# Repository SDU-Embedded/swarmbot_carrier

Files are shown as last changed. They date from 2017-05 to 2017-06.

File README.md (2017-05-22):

# swarmbot_carrier
Repository containing documentation related to the design and operation of the Swarmbot carrier card.

# Revision history
### Rev. 2, May 2017:
* Fixed pinout of the BSS138 MOSFET (A grounded gate pin makes for a boring circuit).
* Swapped the negative and positive inputs on U1 to correctly enable the 3.3V rail. 
### Rev. 1, April 2017:
Initial layout for debugging purposes.

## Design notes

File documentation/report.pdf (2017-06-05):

University of Southern Denmark

MSc in Engineering - Electronics

Individual Study Activity

## Developing the Swarm Bot

Authors:
030192 Mikkel Skaarup Jaedicke 100589 Thomas S. Christensen

Supervisor:
Leon Bonde Larsen

Date: 31-5-2017

## 1 Introduction

A platform for research of flocking behaviour in swarms of robots was developed throughout the bachelor’s thesis, “Investigating Bio-inspired Object Avoidance in a Swarm of Mobile Robots” by Niels A. Hvid and Rasmus
K. Stagsted. Throughout that project an analysis was carried out in order to determine the requirements of the system. This project aims to replace the Raspberry Pi with an FPGA platform, namely a Zynq platform. Using an FPGA/ARM combination is believed to better enable the use of swarm algorithms. Additionally, since the completion of the bachelor’s thesis, a new type of microphone has been procured. This type is digital, as opposed to the previous analogue microphones. Much of the electronics developed for that project is developed so as to work around the shortcomings of the Raspberry Pi, as well as the amplifier circuits required for the microphones. This project will redesign the electronics where necessary in order to accommodate the changes on the platform.

## 2 Analysis

This analysis will seek to expand on the analysis carried out in the aforementioned thesis. Some of the conclusions reached are no longer valid due to the new platform. It is necessary to determine which parts will need redesign and possibly, what new features will need to be added altogether.

### 2.1 Mechanical Platform

The chassis, battery and motors, including their encoders remain unchanged and as such will not be discussed further in this context.

### 2.2 Microphones

As mentioned, a new set of digital microphones has been procured for use with this robot. The previous electronic circuits developed include an amplifier section for the analogue microphones. This is no longer necessary. The analysis did find, however, that the multilateration algorithm is more robust when the microphones are further apart, therefore the new microphones should be placed towards the corners, as was done with the previous microphones.

1

### 2.3 Click Generator

Previously, it was attempted to generate a click using a piezo transducer. The attempt did not manage to produce a sufficiently loud click. A piezo transducer deforms when a voltage is applied to it. A higher voltage increases the deformation. By repeatedly pulsing the transducer with a sufficiently high voltage, it should be possible to generate a sound. Some type of circuit will have to be used to generate the necessary voltage spike.
The sound of a Piezo transducer is amplified when placed in a plastic housing with a small hole to let the soundwaves out. This housing and the size of the hole should be designed to amplify the specific piezo transducer’s resonant freqency. Designing such a housing is infeasable, considering how cheaply a finished product can be procured. A piezo element is generally designed to generate sound with a specific frequency. This can be seen by inspection of the frequency response curve of a piezo transducer. A depiction of a typical response curve can be seen in figure 2.1

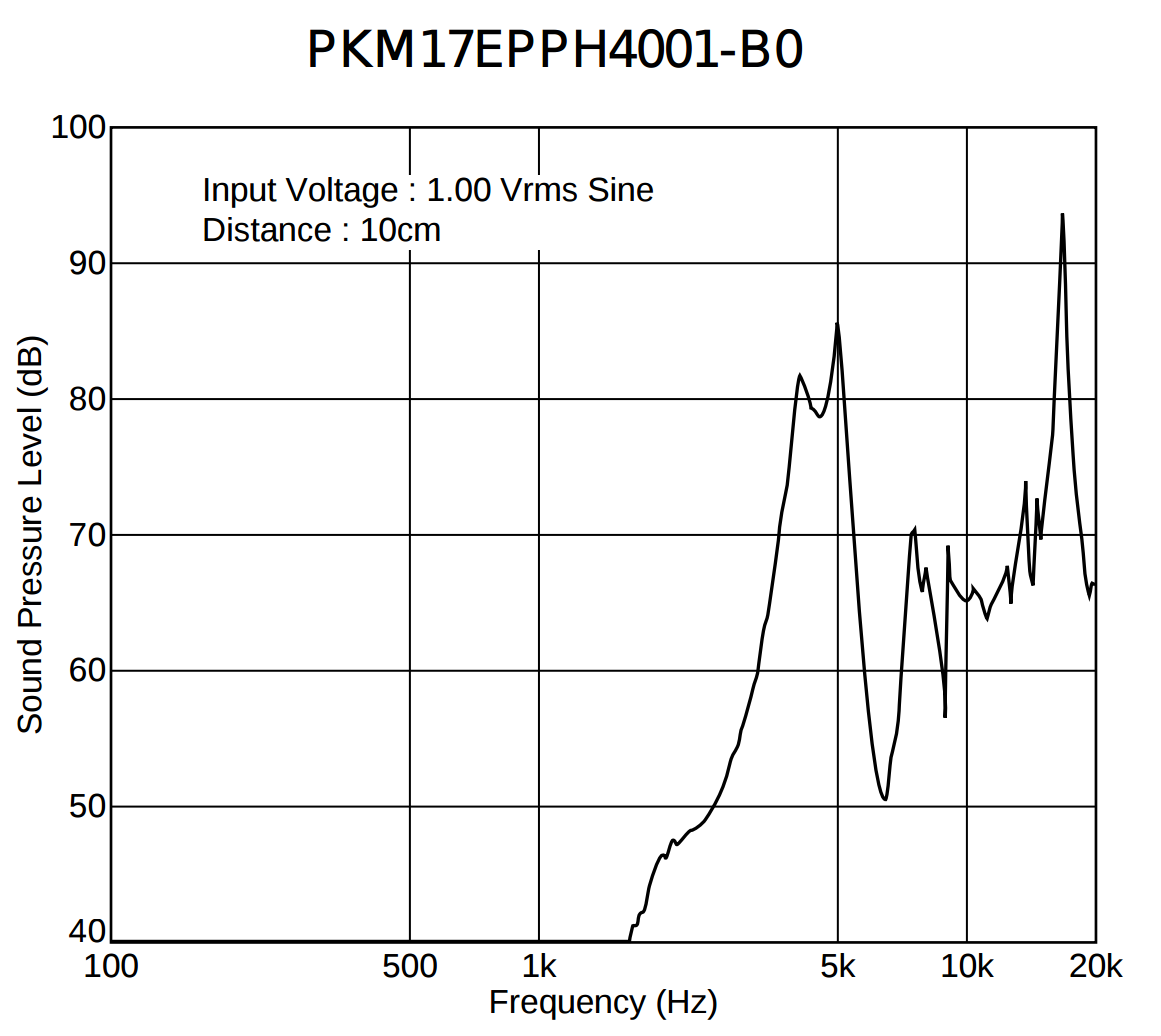
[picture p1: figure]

Figure 2.1: Typical frequency response of a piezo electric transducer. This particular model is most effective at approximately 5kHz and 18kHz.

Generally there are a range of frequencies around the resonant frequency that are at a much higher sound level than the rest of the frequencies. Frequencies not in close range of the resonant frequencies are often attenuated by decades of dB. This makes a normal piezo unfit for generating a click sound as this is approximated by a short frequency sweep. Another option is the piezo speaker that is designed to have the same flat frequency response curve as an ordinary speaker. It is therefore more fit to produce a clicking sound by making a frequency sweep. An ordinary speaker can also

2

be used, but generally they consume much more current to produce the same sound. It was choosen to order three different kinds of sound generators to experiment with sound loudness, clicking sounds and power consumption.

- Piezo element with plastic housing and internal drive circuit [10].
- Piezo speaker in plastic housing without drive circuit [11].
- Miniature speaker [12].

Piezo Element with Internal Drive Circuit

This element produces a sound with a constant frequency just by connecting it to a DC power supply. This is very simply and allows for a minimal interface, but the internal drive circuit makes it impossible to produce a frequency sweep.

Piezo Speaker

This Piezo speaker is designed to have a more flat frequency response and is therefore suitable for producing a frequency sweep. An external drive circuit needs to be developed to test the device as a drive circuit is not included with this product. The developed circuit can be seen in figure 2.2.

D

C

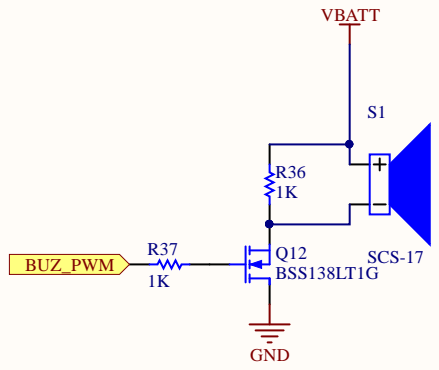
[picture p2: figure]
Q12 BSS138LT1G; SCS-17; VBATT; GND; BUZ_PWM

Figure 2.2: Schematic of drive circuit for piezo speaker.

A mosfet controlled by a PWM pin is toggling current from VBATT to GND and thereby controlling the sound generated by the piezo. By changing the dutycycle of the PWM signal the volume produced can be controlled. A 50%

3

dutycycle yields the highest volume. A resistor is placed in parallel with the piezo speaker as it is capacitive and needs to discharge when the mosfet goes off. The resistor in front of the mosfet is needed to limit the current from the PWM port.
In experiments with the circuit and the piezo speaker, the PWM port was connected to a frequency generator set up to do frequency sweeps. This produced loud and clear clicks.

Miniature speaker

The miniature speaker, as the piezo speaker, needs a drive circuit. The circuit from figure 2.2 was used again and the same frequency generator was used. In this setup the miniature speaker also produces clicks that was audible, but the sound produces was of significantly lower volume. Which was also expected.

Conclusion

It was chosen to use the Piezo speaker with the developed drive circuit as it has the capability of producing a click sound and it produced a significantly greater volume than the miniature speaker in the same setup. Besides that it produces no electro magnetic noise as the miniature speaker does.

### 2.4 PWM Generation

The Raspberry Pi previously used has support only for one PWM channel. In order to fully control the robot, four channels are required. For this reason it was chosen to use an external PWM generator which can be communicated with through I2C. Moving to an FPGA based platform, this is no longer necessary, as it is possible to add as many PWM channels as required in VHDL.

### 2.5 Motor Driver

The BD6222HFP was chosen as the motor driver in the previous project. This is a full-bridge capable of continuously supplying sufficient power to drive the motors on the robot. This driver chip is maintained in the new design.

4

### 2.6 Current Limitations

A number of fuses were added to limit the current to the motors as well as the current draw from the battery. The battery however, includes a “safety board” which limits the maximum possible current draw, making this fuse irrelevant. The fuses on the motors can be excluded by instead running a check in software such that when a voltage is applied, the encoder signal must represent movement, or the voltage will be cut. Allowing overcurrent for a short period will not damage the motors and therefore this approach is acceptable.

### 2.7 Electronics Board

In order to accommodate the new electronics a new board will have to be designed. The board must support a number of components and circuits, listed below.

- Motor controller: The BD6222HFP, a full-bridge motor controller, is used to generate the drive signals for the motors.
- Piezo: Generating a click is done using a piezo transducer. A transducer with an external drive circuit will be used.
- 5V DC/DC Converter: A DC/DC converter will be used to generate the 5V rail necessary to drive the embedded platform.
- Connections: A number of connections has to be present on the board. Passthrough for the microphone add-in board. Passthrough for the motor encoders. Connection for battery.
- Debug LEDs: Support for four LEDs for debugging is required. The necessary drive circuitry must be added.
- Microphone board: A microphone board has been developed at SDU, supporting up to four SPH0641LU4H-1 digital microphones. The board must allow for interfacing with this microphone board.

### 2.8 Power Calculations

In the previous project it was chosen to use linear regulators to supply the 5 and 3.3V rails. This project will analyse whether the added cost of using switch-mode converters is worthwile considering the possible extra battery life. It will be analyzed how much power is drawn from the 5V- and

5

battery voltage-rails and what the expected additional battery life will be when using a switch-mode converter. It has been found that the DC/DC converter, PTH08080WAH, is suitable for this project and this component’s specifications will be used for calculations.

5V Rail (VCC)

The following are powered by VCC:

- Microphones including circuitry, 11mA
- Zynqbased embedded platform, 500mA
- Two motorcontrollers, 5mA
- Six LEDs, 120mA

The current estimation of the microphones, motorcontrollers and LEDs are based upon datasheet values. Whereas the current estimation for the Zynqbased platform is based upon current measurements from a previous project. The current drawn of the Zynq is obviously dependent on the program running, the amount of logic in use, the number of GPIO in use and so on. All of these are unknown at time of writing. 500mA is by no means the maximum current draw that can be expected from a Zynqbased platform, as the MicroZed draws 1.7A at 85% utilization [4].
These estimates bring the total current draw of the VCC rail to 636mA

Battery Voltage Rail (VBATT)

The motors will be running directly from VBATT. To measure the current drawn by the motors and motorcontrollers a small test was conducted. Three different voltages were applied to the motors using a laboratory power supply. Voltage and current measurements were made with the robot driving. The results are shown in table 2.1.

Table 2.1: Voltage, current and power of motors and motorcontrollers measured at different velocities.

Velocity | Voltage, [V] | Current, [mA] | Power, [W]
Low | 1 | 220 | 0.2
Medium | 5 | 305 | 1.5
High | 8 | 350 | 2.8

6

The piezo speaker is powered by VBATT as well, but it produces sound only for a few milliseconds at a time and in addition, with a very power. For this reason, this current draw is neglected throughout the remainder of the discussion.

Power Dissipation

When using a linear voltage regulator the power dissipated in the component can be calculated using:

PLR = (Vin − Vout) · Iload

The power dissipation in the linear regulalator can be found using the current estimation at 5V and the fact that the battery has a nominal voltage of 7.4V:
PLR = (7.4[V ] − 5.0[V ]) · 0.636[A] = 1.5[W]

If a switching regulator is used the voltage conversion will have a significantly higher efficiency. The pth08080w has a typical efficiency of 93.5% at 5V [6]. The power dissipated in the DC/DC converter would be:

PSW = Vin · Iload · (1 − η)

PSW = 7.4[V ] · 0.636[A] · 0.065 = 0.3[W]

The total power drawn at the 5V rail is:

P5V = 0.636[A] · 5[V ] = 3.2[W]

Based on the measurements of voltages and currents of the motors and motorcontrollers, the power dissipated were calculated to be as in table 2.1. The total power usage can be calculated as the sum of the combined powers.

PT = Preg + Pmotor + P5V

Calculating the total power usage at low velocity and using a linear regulator yields:
PT,LR = 1.5 + 0.2 + 3.2 = 4.9[W]

The total power at the three velocities is calculated using a linear regulator or a DC/DC converter and is shown in table 2.2.

7

Drive Time

The amount of energy the battery can store should be calculated in order to calculate the drive time of the robot. The batteries have a rated capacity of 2600mAH [9]. Converted to Joule:

Ebat = 2.6[AH] · 7.4[V ] · 3600 = 69.3[kJ]

The drive time can then be calculated:

T =

Ebat
PT

Specifically for low velocity and using a linear regulator:

TLR =

Ebat

PT,LR

=

69.3[kJ]
4.9[W]

= 14143[s]

Which corresponds to 3.9h. The calculation is done for all scenarios and the results are shown in table 2.2. Finally the extra drive time obtained by using a switching regulator rather than a linear regulator is calculated and shown in percent in table 2.2.

Table 2.2: Total power and drive times using linear regulator or switching regulator. The obtained extra drive time by using a switching regulator is given in percent.

Velocity | PT,LR [W] | PT,SW [W] | TLR [h] | TSW [h] | % more T
Low | 4.9 | 3.7 | 3.9 | 5.2 | 33
Medium | 6.2 | 5 | 3.1 | 3.8 | 23
High | 7.5 | 6.3 | 2.6 | 3.1 | 19

Using a switching regulator yields a minimum of 19% more drive time compared to using a linear regulator. On the basis of the results it is concluded that using a switching regulator is worth the additional cost.
Note that these results are very conservative estimates. The more power is being drawn from VCC, the more the benefits if the switch-mode converter would show.

### 2.9 Embedded Platform

Previously a Raspberry Pi was used to power the platform. As mentioned, it has been requested that the system is ported to a Zynq platform. Currently

8

available to the authors are the Zybo, MicroZed and Zynqberry platforms. All three are based around the Zynq-7010 chip. A number of GPIO ports are required; seven pins for PWM for the motors, four pins for encoders, four pins for microphones, one for a piezo transducer and six for two RGB LEDs. This amounts to a minimum of 22 pins required. Below is an overview of the pros and cons of the two platforms.

- Zynqberry: As the name implies, this platform is made to conform with the physical layout of the Raspberry Pi. Using this platform would allow the reuse of the mounting solution developed for the Raspberry Pi. At 26 total GPIO pins, the Zynqberry can supply the required GPIO, but has nearly no pins if extra sensors or hardware is needed in the future. When searching for information on this platform it was found that there is not a lot of documentation made by neither the manufacturers or the community.
- Zybo: This platform is significantly larger than the Zynqberry. The different form factor requires that a new mounting solution is devised. Additionally, the increased size means that the board will have to be mounted above the tracks to avoid interference. While this is an inconvenience, it should not pose an issue in collisions as the edges of the board are still within the bounds of the robot. At 48 total GPIO pins, the Zybo can supply the required GPIO.
- MicroZed: This platform is within the confines of the robot platform, but has a different formfactor than the Raspberry Pi and therefore the mounting solution would need a re-design. It can be used as a stand-alone evaluation board, but needs to be combined with a carrier card if the PLs I/O pins are to be used. This is because the I/O banks on the Zynq chip need external powering, supplied by the carrier card. The 100 I/O pins on the MicroZed are accessed through two micro headers. The company behind the MicroZed also ship different carrier boards that can be used. If a custom carrier board is needed, circuitry for control signals and power needs to be developed. The online documentation for the MicroZed and carrier card is thorough and plentyfull including user guides, hardware guides, schematics and bill of materials.

The MicroZed is found to be the best choice for this project. Mainly because it is within the confines of the robot platform, gives access to 100 I/O pins and has solid documentation.

9

MicroZed Carrier Card

It was decided to design a custom carrier card for the MicroZed. A number of the requirements, which are outlined in this section, would result in additional boards having to be connected to the Avnet carrier cards anyways and so it was decided to combine all of the functionality on one board. As mentioned, this section will define the requirements for the MicroZed carrier card to be designed. Avnet provides a carrier card design guide [1] that describes some of the requirements. It describes how to utilize the Zynq chip on the MicroZed board. In this project, only a number of general I/Os are needed. Two ADCs are added for the possibility of utilising them at a later stage. This carrier card however, is expected to be used across a number of other, yet undefined projects. For this reason the card is designed in a more general fashion, rather than specifically for the swarmbot. Below is a list of the features the carrier card is designed to support.

- ADC, not used on the swarmbot.
- Motor Drivers capable of driving the swarmbot.
- Support for the digital microphone board, developed at SDU.
- Support for click generator.
- Passthrough of MicroZed GPIO.
- Debug LEDs.

These points are the features that the user will be presented with when using the board. In addition to these, a number of requirements are set in the afforementioned design guide:

- Anti-aliasing filters for ADC inputs.
- Power for MicroZed board and Zynq I/O banks 34 and 35.
- Correct power sequencing on boot/shutdown.
- Microheader connection to MicroZed.

The following sections will outline how each of these points are addressed in the design of the carrier card.

10

## 3 Design and Implementation

Avnet supplies a MicroZed breakout carrier card as a reference design for designing carrier cards. All of the schematics and layout documents are made publicly available and will, in conjunction with the carrier card design guide [1] form the basis for the design of the swarmbot carrier card.

### 3.1 Power Requirements

A carrier card needs to provide the following voltages for the MicroZed:

- Vin = 5V
- Vccio,13 (Voltage logic level for I/O bank 13)
- Vccio,34 (Voltage logic level for I/O bank 34)
- Vccio,35 (Voltage logic level for I/O bank 35)

The different I/0 banks can be operated at different voltage levels. According to [2], the possible logic levels are 1.2V, 1.5V, 1.8V, 2.5V, and 3.3V.
It was chosen to supply all I/O banks with a voltage level of 3.3V as the vast majority of hardware used is available at this voltage. Additionally, it simplifies both the circuitry, as well as the use of the board.

Vccio = Vccio,13 = Vccio,34 = Vccio,35 = 3.3V

The schematic and components used for the generation of the 3.3V rail is available in [3] and [13] and will not be discussed further as this is not the design of the authors. Since the swarmbot is designed to be powered from a 7.4V LiPo battery, the 5V rail has to be generated from this rail. As the voltage of a battery is not static, the converter will have to be able to supply the required voltage throughout the entire discharge cycle. In order to determine the maximum and minimum voltages of the battery, a discharge curve was created. More detail on the test done to create the curve can be found in section 4.3, but the result is repeated in figure 3.1 for convenience. Here it can be seen that the maximum voltage once fully charged is 8.4V while the minimum voltage when discharged fully is approximately 5.5V, as per the documentation of the battery [9]. Attempting to procure a DC/DC converter capable of maintaining a stable 5V output with an input voltage of just 0.5V higher may prove to be an expensive endeavour. The curve reveals that the voltage remains above 6V for ≈85% of the discharge cycle, even when discharging at 4A, far above what the carrier card will be capable

11

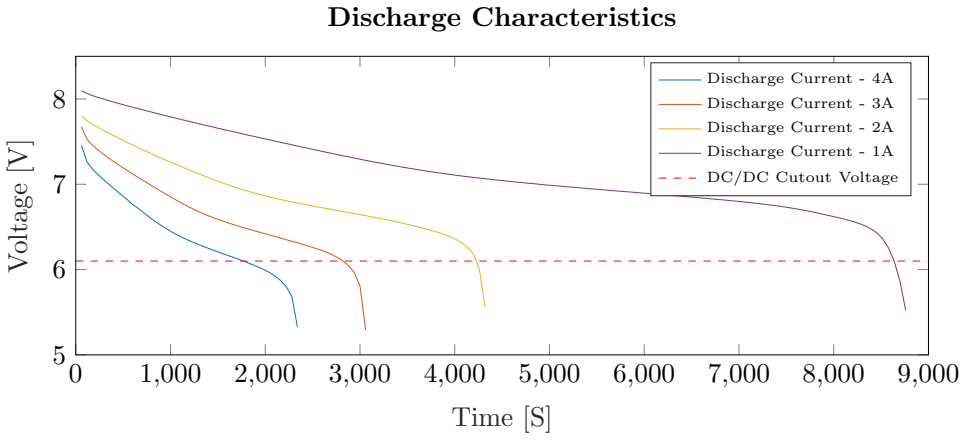
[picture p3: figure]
Time [S]; Voltage [V]; Discharge Characteristics; Discharge Current - 4A; Discharge Current - 3A; Discharge Current - 2A; Discharge Current - 1A; DC/DC Cutout Voltage

Figure 3.1: Discharge curve of the Ansmann 18650 2S1P Li-Ion battery used to power the swarmbot.

of handling. For this reason, this will be the target minimum input voltage of the DC/DC converter. According to [4] the estimated maximum power draw of the MicroZed is 1.7A at 5V. This is assuming 85% utilisation of PL and a conservative 80% efficiency of the converters. The estimate made by Avnet is made with the Zynq-7010 in the Xilinx Power Estimator (XPE) [5]. The MicroZed used for the swarmbot project, however, is equipped with the Zynq-7020, a slightly larger chip. Running the same scenario, 85% utilisation, in XPE reveals that the 7020 draws 2.3W, just 0.1W more than the 7010, a marginal difference in the total power budget. In addition to the MicroZed, also the debug LEDs and the microphone board are powered from this rail, adding an estimated ≈150mA extra current draw. In summary, these are the requirements for the DC/DC converter used for generating the 5V rail:

- Must function across the entire voltage range of the battery, 6V to 8.4V.
- Should be able to supply at least 1.85A at 5V.

Below is a discussion of the various choices made in the design of the circuitry of the 5V supply.

12

Designing the 5V Rail

The PTH08080WAH [6] closely meets these requirements at a maximum power delivery of 2A/10W/5V. The device is designed to have a wide input range, accepting Vin=Vo+1.1V to 18V. At the required 5V this translates to an input range of 6.1V to 18V. This is of course slightly higher than the desired 6V, but even at the maximum discharge rate, estimated at 2.2A-2.3A, with the MicroZed drawing its maximum current and the motors running at full speed, there would still be approximately 70 minutes of operation per charge. Vo is determined via an external resistor Rset. A formulae is provided to calculate the exact Rset needed for a given voltage, however a large table of common values is already calculated. According to this table, Rset=353Ω results in 5V. 353Ω is not a standard value, choosing 348Ω instead yields 5.01V, which is fine for this application.

The circuit appertaining to this component can be seen in figure 3.2. This is the standard application circuit as shown in the datasheet (figure 10 [6]). According to the datasheet, the minimum recommended input capacitance is 100µF. Of the capacitors on the list of recommended capacitors, also given in the datasheet, the 20SVP150M was chosen. It is rated for 20V, sufficient for this application, and has a capacitance of 150µF.

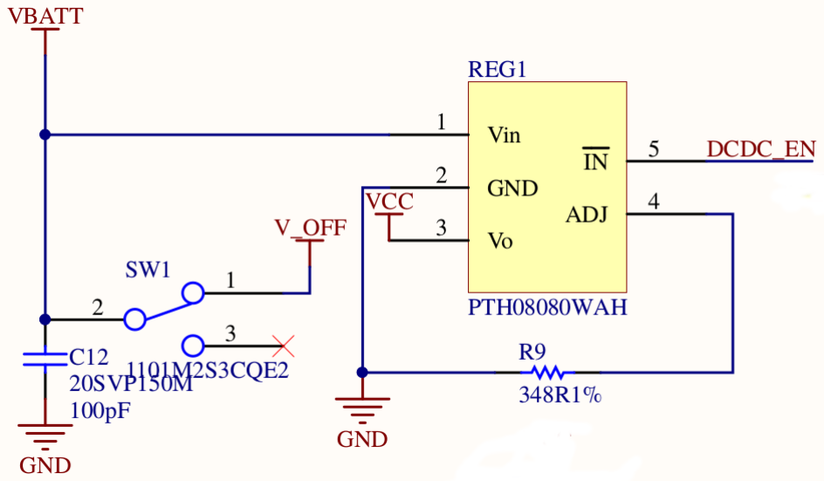
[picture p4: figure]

Figure 3.2: Circuit for generating VCC, the 5V rail.

### 3.2 Power Up Sequence

According the carrier card design guide, [1], a carrier card needs to adhere to a specific power up sequence in order for the MicroZed to turn on correctly. On power up, MicroZeds PWR EN signals need to be pulled high on the carrier card, to enable power to the MicroZed. This is done with a pull-up resistor

13

as shown in figure 3.3.

38LT1G

EN

100nF

C18
C0805

Q2
BSS138LT1G

GND

VCC

GND

V_OFF

POWER_EN POWER_EN

D4

18TQ045

R12
1K

R15
3K92 1%

R20
430R 1%

R19

680R 1%

Figure 3.3: Circuit for proper power sequencing on MicroZeds PWR EN.

When the MicroZed has powered up its internal DC/DC converters and is ready to receive voltage on its I/O banks VCCIO EN will go high. VCCIO EN has a logic level of 1.8V and the signal is therefore fed to a comparator that outputs a 5V signal to a DC/DC converter when VCCIO EN is high. The DC/DC converter is configured to produce a voltage level of 3.3V that is connected to VCCIO. This circuitry can be seen in figure 3.4.

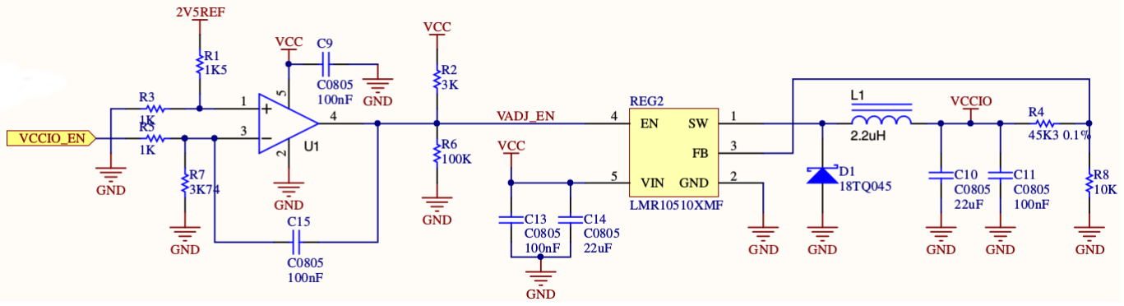
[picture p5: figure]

Figure 3.4: Circuit for proper power sequencing on I/O banks.

### 3.3 Power Down Sequence

A power down sequence is also described in [1], that needs to be followed to ensure signal integrity while powering down. The signals VCCIO EN, DCDC EN and PWR EN should be pulled down in that order when powering off. The

14 signals are pulled down by mosfets controlled by the V OFF signal. When the power switch on the carrier card is in off mode, the battery voltage is connected to the V OFF rail thereby turning the mosfets on and pulling the signals down. The correct sequence is maintained by charging capacitors on the gate side of the mosfets thereby creating a delay. Such a mosfet circuit is shown in figure 3.3.

### 3.4 Analog to Digital Converter

The Zynq 7-series FPGA’s are equipped with a dual, 12 bit ADC, yet has only one dedicated analog differential pair, VP 0 and VN 0. See figure 3.5 for an overview of the XADC architechture If more ADC channels are needed, any of the 16 auxiliary analog inputs (AAI) can be used. These are placed on I/O bank 35 which, as the rest of the I/O on the swarmbot carrier card, is supplied with VCCIO=3.3V. Once selected, a multiplexer applies each signal to the ADC’s in turn. For this reason any signal on the AAI can never go above VCCIO to avoid damaging the inputs. On the swarmbot carrier card the dedicated analog pins, as well as three AAI pairs are routed to the ADC header (CON4). The signals VAUX P0 and VAUX N0 on JX1 are the dedicated analog inputs and can be used on its own. The remaining three pairs are AAI and must be multiplexed if the user wishes to use them. It should be noted that due to the anti-aliasing filters, these pairs cannot be used as digital I/O on the swarmbot carrier card. These anti-aliasing filters are required in order to filter out high frequency noise in the differential pairs and should be placed as closely to the Zynq as possible, in this case, that is next to the connectors JX1 and JX2, the main connectors to the MicroZed. Figure 3.6 from [?] illustrates a simple measurement setup and the anti-aliasing filter. R1 and R2 form a voltage divider, creating a 1V signal. R5 is matched to the parallel impedance of R1||R2. Resistors R3, R4 and the capacitor C1 can be adjusted to change the settling time of the circuit. [7] gives equation 3.1 which can be used to calculate the settling time and by that determine the maximum sampling frequency.

Ts = ln 2resolution+1
·
R1 · R2
R1 + R2

+ R3 + R4 + R5

·C1 = 4.9 · 10⁻⁶
[S] (3.1)

### 3.5 Buzzer Solution

As described in section 2.3 it was found that the best solution for creating a clicking noise on the platform was to use a piezo speaker with a drive circuit

15

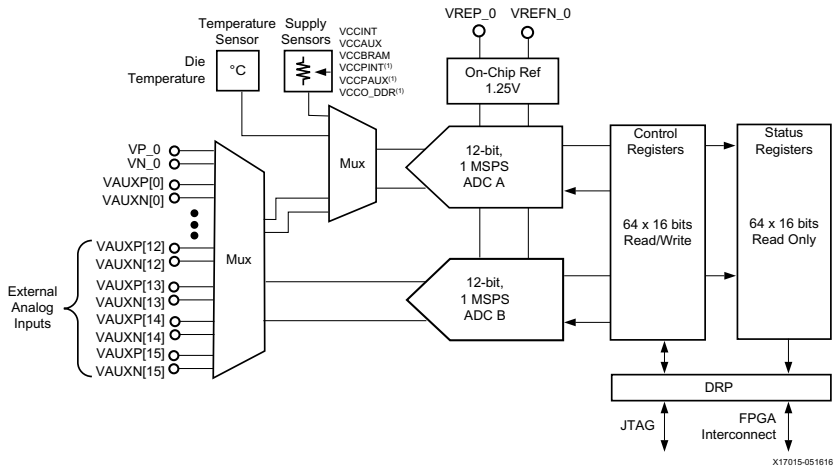
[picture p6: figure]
X-Ref Target - Figure 1-1; 'LH 7HPSHUDWXUH; 7HPSHUDWXUH 6HQVRU; 6XSSO\ 6HQVRUV; ELW 0636 $'&$; ELW 0636 $'&%; [ELWV 5HDG:ULWH; [ELWV 5HDG2QO\; &RQWURO 5HJLVWHUV; 6WDWXV 5HJLVWHUV; 2Q&KLS5HI 9; ,QWHUFRQQHFW; ([WHUQDO $QDORJ ,QSXWV

Figure 3.5: XADC Block Diagram from Xilinx ADC userguide [7].

and a PWM signal. But because there has been made no further investigation into what sound level is needed and what the frequency spectrum of the generated click is, it was decided to leave the circuitry out of the carrier card. Furthermore the sound source should be placed in the center of the robot to ease localization of the robot, but the design of the carrier card did not allow this. Therefore it was decided to include a header providing access to two IO ports, ground and VBATT. The header is shown in figure 3.7. Two IO ports are needed if differential drive of the piezo is wanted. Two holes were added to the carrier card to allow for fixture of the external piezo and drive circuit.

### 3.6 Pinout

The complete pinout can be found at [15] but a few cases are mentioned here for completeness. Some pins on the GPIO headers, (CON5, CON6) are routed to multiple locations, this increases the amount of available IO, but also introduces some possible traps for the user. Below is a list outlining the pins in question.

- MIC *: All of the ports related to the microphone board are routed both to the microphone header, CON3, and one of the GPIO headers, CON5. These ports should not be used as IO if the microphone board is connected.

16

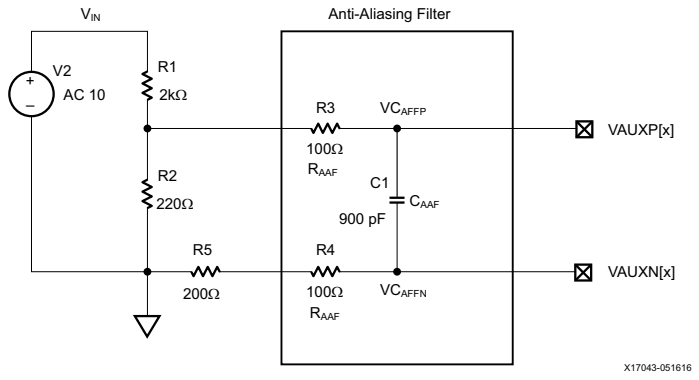
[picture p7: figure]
X-Ref Target - Figure 6-3; VIN; Anti-Aliasing Filter; RAAF; VCAFFP; VCAFFN; CAAF; VAUXP[x]; VAUXN[x]

Figure 3.6: Anti-Aliasing diagram from Xilinx ADC userguide [7].

1
2
3
4

P4

Audio Header

BUZ_PWM1
BUZ_PWM0

VBATT

GND

Figure 3.7: Audio header on the carrier card.

- ENCxy: These ports are wired to both the CON1 or CON2 for channel 0 and 1 respectively, and CON6. The connection to the GPIO header is for measurement only.
- Mx PWMy: These ports are wired directly to the motor controller and should not be used as IO. The connection to the GPIO header, CON6 is for measurement only.
- BUZ PWMx: These signals are wired to the audio header, P4, and to one of the GPIO headers, CON6. These ports should not be used as IO if a buzzer is connected.

In addition to these signals it should be noted that the four signals marked JXx TPyy are meant as test signals. They are GPIO ports but are placed on a seperate header to allow for easier access with measurement equipment.

17

### 3.7 Choice of Components

As mentioned, the choice of components is largely based upon the Avnet carrier card. Generally the same components were chosen but due pricing, availability or minimum order size, some components were changed to similar ones. Table A.1 and A.2 in appendix A explains what components were chosen and why.

### 3.8 Swarmbot Carrier Card Layout

The layout of the swarmbot carrier card was done using Altium Designer. From an early stage it was decided to have the board manufactured by a professional outlet as this would both greatly ease the layout process and, hopefully, minimize the potential points of failure in debugging process. The former, a simpler layout process, is expected for a number of reasons outlined below:

- Mutlilayer Board: Due to the size constraints of the board it is desirable to minimize the number of traces that are required to be routed on the board. Creating a 4-layer board means that the two middle layers can be GND and VCC, allowing every connection to either of these plains to be done using a simple via.
- Feature Size: The manufacturing method used at SDU is not reliable at tracewidths below 20mil and all vias must be drilled by hand, resulting in signal traces being far wider than what is actually required. The manufacturer used to produce the swarmbot carrier card [8] allows traces as low as 8mil and vias at 12mil.
- Plated Vias: The vias created by the manufacturer are plated with copper, meaning that, when using throughhole components the trace can be routed on both the top and bottom layers, without the use of additional vias. This greatly reduces the number of vias required for the layout.

Finally, as was alluded to in the previous paragraphs, the manufacturing process at SDU is not particularly robust and often requires several attempts before the correct combination of incantations, candles and luck is found and a fully functional board is created.

The board has three trace widths: 40mil for VBATT, 20mil for VCCIO and 8mil for the remaining signal wires. Mostly, the size of the board is due to

18 the number of connectors that are required. For this reason there is plenty of room for components and generally capacitors and resistors were chosen with a 0805 footprint. The anti-aliasing filters described in section 3.4 are required to be placed close to the Bergstak connectors (the connector for mounting the MicroZed), which has a 0.8mm pitch. Using 0805 components here is infeasible due to size and it was decided to use 0402 instead.

## 4 Verification

Throughout this section the verification of voltage-rails, desired power-up and power-down sequences are made in order to avoid damaging the MicroZed when first connecting it. After these steps, the correct functionality of the MicroZed while connected to the carrier card is verified. In addition, the functionality of the different IO ports on the carrier are verified to ensure that the carrier card functions as expected. This section will describe the work done to debug and verify the functionality of the carrier card.

### 4.1 Carrier Card Debugging

After soldering of all the components it was found by measurement that the board was not functioning correctly. The debugging of the board will be described in this section.
The carriercard is designed to allow for measurement of the voltage-rails on the powerheader, P1, without connecting the MicroZed. Specifically the J1 jumper should be present to simulate the VCCIO EN signal from the MicroZed. All voltages on the powerheader were measured with an oscilloscope whilst toggling the power switch. VCC should switch between 0V and 5V, which it was not, leading to the conclusion that the circuitry handling the enable signal, DC/DC EN, to the REG1 DC/DC converter could be faulty. By inspection, it was found that the footprint of the mosfets Q1,Q2 and Q3 was wrong. A temporary fix was done by rotating the components, soldering them in place using signal wires. The power switch now toggled both the VCC rail and the 2.5V rail on and off.
Measurements of VCCIO during powerup showed that it immediately went to approximately 3.3V, but then discharged slowly towards zero voltage. The enable signal, VADJ EN, was low even though the input voltages were measured to be as expected. This lead to a thorough examination of the component and the schematic and it was found that the input signals should be switches. The input signals were switched, which fixed the issue and made the VCCIO voltage follow the position of the powerswitch.

19

Measuring the voltage level of VCCIO showed it to be 3.4V rather than the expected 3.3V. This was due to placing a 47kΩ resistor as R4 instead of a 45.3kΩ as specified in the schematics. Even though 3.4V is within spec, it was decided to parallel the 47kΩ resistor was with a 1.5MΩ resistor to yield a resistance of 45.6kΩ and a voltage of 3.33V.

### 4.2 Carrier Card Power Sequencing

As described in sections 3.2 and 3.3 the carrier card is designed to provide a specific power sequence on startup and shutdown.

Startup

To verify the proper startup power sequence of the Swarmbot carrier card the signals VCC, 2V5REF, VCCIO EN and VCCIO were measured and plotted in figure 4.1a. [1] dictates that POWER EN signal must be pulled high on powerup, which was measured to be true. VCCIO EN is produced by the MicroZed and is plotted in figure 4.1a. It can be seen that VCCIO EN rises to its logical level, 1.8V, then goes low for a while and hereafter goes high, which is not the expected behavior. To determine if this behavior was caused by an issue on the Swarmbot carrier card the value of VCCIO EN on the AVNET carrier was measured at startup when connecting the MicroZed to the AVNET carrier card. The two measurements of VCCIO EN at startup is plotted in figure 4.1b. It can be seen that the two datasets are nearly identical concluding that the Swarm and AVNET carrier card yields the same behavior. As VCCIO EN has the same behavior when connecting the MicroZed to the AVNET carrier it is believed to be non problematic.
The converter providing VCCIO should be enabled by VCCIO EN. By inspecting figure 4.1a it is verified that when VCCIO EN is high the converter providing VCCIO is enabled and VCCIO rises towards its final level of 3.3V. It is also verified that 2V5REF reaches its expected voltage level of 2.5V.

20

0 | 2 | 4 | 6 | 8
| | | | ·10⁻³

0

2

4

6

8

Time [S]

Voltage [V]

Startup Sequence, Swarmbot

VCC

2V5REF

VCCIO EN

VCCIO

(a) Signals on the Swarm carrier card at startup.
0 | 2 | 4 | 6 | 8
| | | | ·10⁻³

0

2

4

6

8

Time [S]

Voltage [V]

Startup Sequence, VCCIO EN

VCCIO EN, SWARM

VCCIO EN, AVNET

(b) VCCIO EN at startup on Swarm and AVNET carrier card. Data is shifted in time for clarity.

Figure 4.1: Measured signals at startup.

Shutdown

To verify the proper shutdown power sequence of the Swarm carrier the signals POWER EN, DCDC EN, VCCIO EN and V OFF were measured and plotted in figure 4.2. V OFF switches from 0 [V] to the battery voltage, when setting the power switch in off mode. Then the signals VCCIO EN, POWER EN and DCDC EN should be pulled low in that order. Figure 4.2 shows that to be true.
It should be noted that figure 4.2 only shows the first few microseconds after toggling the power switch. In figure 4.3 the first millisecond is shown and it can be seen that the switch creates quite a lot of bouncing on V OFF. The bouncing could be removed by designing and inferring a low pass filter to the circuit, possibly with a Schmitt trigger circuit to generate a clean edge. This, however, adds additional cost and complexity to the board. Until deemed necessary, this will not be explored futher.

### 4.3 Discharge Curve of the Ansmann 2S1P

In an effort to quantify the possible runtime of the system, a discharge curve was made for the Ansmann 2S1P Li-Ion battery used in this project. Making the discharge curve was done by fully charging the battery using the

21

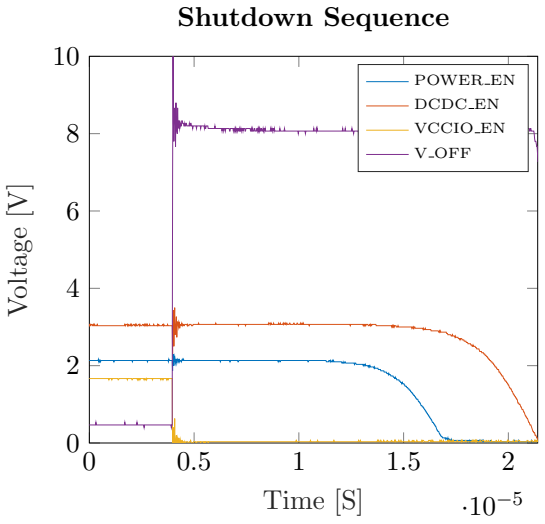
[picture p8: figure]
Time [S]; Voltage [V]; Shutdown Sequence; POWER EN; DCDC EN; VCCIO EN; V OFF

Figure 4.2: Measured signals on the Swarm carrier card at shutdown.

Swallow AC/DC 2 charger. This charger is capable of charging a variety of batteries, following the specific charge curve for each technology. As is expected from a 2-cell Li-Ion battery, the no-load voltage once fully charged is ≈8.4V. After charging, the battery is connected using a DC Electronic Load (model number: EA-EL 3160-60). The load is set at constant current mode and the current set. The battery is equipped with undervoltage protection that turns off the output once the voltage dips below 5-5.5V, in spite of this, it was decided to calculate the theoretical duration and run the test for that amount of time. At 2600mAh it will take 2600mAh/4000mA = 0.65h or, in human terms, 39 minutes, to discharge the battery. For the sake of completion, the trial is repeated for 4, 3, 2 and 1A. The result can be seen in figure 4.4. As discussed in sections 2.8 and 3.1, the maximum current draw of the platform at the battery is approximately 2.2A. Although it should be noted that this is a theoretical maximum and that it is unlikely that this will actually be reached.

As with any battery, due to the internal resistance of the battery the voltage seen at the terminals depends heavily on the current being drawn. The platform will remain functional so long as the voltage remains above 6.1V, the minimum voltage required to maintain VCC, the rail supplying the MicroZed. The maximum speed of the motors will however decline as the battery dis-

22

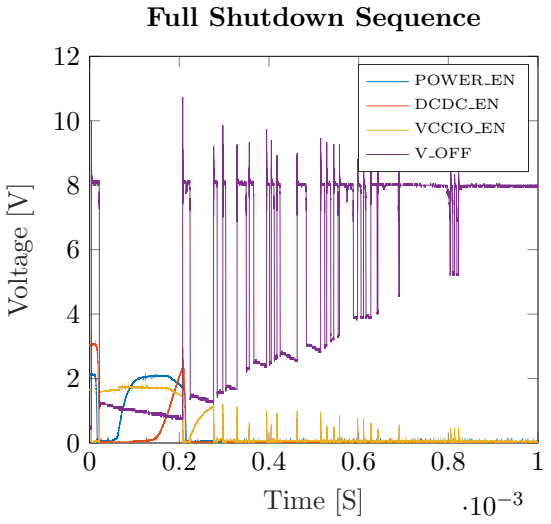
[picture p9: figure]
Time [S]; Voltage [V]; Full Shutdown Sequence; POWER EN; DCDC EN; VCCIO EN; V OFF

Figure 4.3: Measured signals on the Swarm carrier card at shutdown. Full sequence is shown.

charges. From table 4.1 it can be seen that discharging at 2A will give 4200 seconds or 70 minutes of use. Note that the graphs were acquired using two batteries in order to shorten the time required to finish the test. This may have a marginal impact on the results, but is assumed to be irrelevant.

Current [A] | 4 | 3 | 2 | 1
Time [S] | 1740 | 2820 | 4200 | 8640

Table 4.1: Table showing the discharge current and the time before the cutout voltage of the DC/DC converter is reached.

23

Figure 4.4: Discharge curve of the Ansmann 18650 2S1P Li-Ion battery used to power the swarmbot.

IO ports

To ensure the functionality of the IO ports and the MicroZed in general two tests were performed. In the first test a VHDL program was written to turn on an LED connected to an IO port. The test was successful, which led to the conclusion that the PL part of the MicroZed and the IO port are in working order.
In the next test a C program was written to make an LED blink. This test also succeeded, which led to the conclusion that both the PS and PL part of the MicroZed are functioning properly.

Conclusion

The problems on the carrier card were found and fixed through systematic debugging. The carrier card has the wanted powerup and powerdown sequence which was measured using an oscilloscope. Bouncing was seen by the power switch on shutdown. A low pass filter and a schmitt trigger was suggested to alleviate this issue, but it was decided not to implement the solution. A small experiment was conducted in order to get some data on the discharge behaviour of the batteries. This experiment revealed that the platform is likely to see at least 70 minutes of use, possibly more. The PS, PL and IO functionalities of the MicroZed when connected to the carrier were verified through tests.

24

## 5 Conclusion

This project develops on the work done in the bachelor thesis “Investigating Bio-inspired Object Avoidance in a Swarm of Mobile Robots” with the main goal of replacing the Raspberry Pi with a Zynq based platform. It was decided to keep the mechanical platform, battery, motors, motor drivers. Fuses were excluded as the batteries include a ”safety boards” and software can be used to protect the motors. Tests were made to find the sound producer best suited for making a clicking noise on the platform. It was found that a piezo speaker is the best choice, but it was not included on the board to allow for further testing, before making the final decision. A switch-mode DC/DC converter is included as tests and calculations showed that a minimum of 19% extra drive time is gained when using this component instead of a linear voltage regulator. It was decided to use the MicroZed Zynq platform rather the Zynqberry or the Zybo. The MicroZed was chosen as it has plenty of I/O pins, has a solid documentation and it is within the confines of the robot platform. When using the MicroZed a carrier card is needed to power the I/O banks and give access to I/O pins.

It was decided to design such a carrier card and include all electronic for the project on it. The PTH08080WAH converter was chosen and test showed that at least 70 minutes of use can be expected from the robot. It was chosen to supply all I/O banks with 3.3V and circuits were designed to ensure correct power up and power down sequences. Four pairs of anti-aliasing filters were added to enable use of the on-chip ADCs. The carrier card layout was done using Altium Designer and it was decided to have the board manufactured by a professional outlet to allow for a multilayer board, small feature size and plated vias.

After receiving and soldering the designed carrier cards, it was found that the board was not functioning correctly. Thorough physical debugging and fixing of errors led to a correctly functioning board. Correct power up and power down sequences were verified by measuring voltages on the included power header. Verification of main features of the board, such as I/O pins, was made by performing small ”Hello World” style programs in C and VHDL.

In hindsight, it is clear to the authors that the decision to develop a MicroZed carrier card resulted in many hours being spent on this, rather than developing a robot, but it led to a very valuable exercise in the development of a professional layout of PCB and, hopefully the beginning of a platform

25 that can be used by future students.

In addition to the work enclosed herein, documentation such as pinout, schematic and layout, including the entire Altium project, can all be found on the SDU-Embedded:swarm bot github [14].

26

## References

[1] AVNET, | 2014, | MicroZedTM | Carrier | Design | Guide, | http:
//zedboard.org/sites/default/files/documentations/ MicroZed_Carrier_Design_Guide_rev_1_5.pdf (http://zedboard.org/sites/default/files/documentations/MicroZed_Carrier_Design_Guide_rev_1_5.pdf)
[2] Xilinx, 2016, Zynq-7000 All Programmable SoC: DC and AC Switching Characteristics, https://www.xilinx.com/support/documentation/data_sheets/ds187-XC7Z010-XC7Z020-Data-Sheet.pdf (https://www.xilinx.com/support/documentation/data_sheets/ds187-XC7Z010-XC7Z020-Data-Sheet.pdf)
[3] AVNET, 2013, Microzed Breakout Carrier Card Schematics Rev A, http://zedboard.org/sites/default/files/documentations/MBCC-BKO_RevA_Schematic_131114.pdf (http://zedboard.org/sites/default/files/documentations/MBCC-BKO_RevA_Schematic_131114.pdf)
[4] AVNET, 2017, Microzed Zynq Evaluation Kit and System on Module Hardware User Guide version 1.7, http://zedboard.org/sites/default/files/documentations/5276-MicroZed-HW-UG-v1-7-V1. pdf (http://zedboard.org/sites/default/files/documentations/5276-MicroZed-HW-UG-v1-7-V1.pdf)
[5] Xilinx, 2017, Xilinx Power Estimator (XPE), https://www.xilinx.com/products/technology/power/xpe.html (https://www.xilinx.com/products/technology/power/xpe.html)
[6] Texas Instruments, 2013, PTH08080W 2.25-A, Wide-Input Adjustable Switching Regulator http://www.ti.com/lit/ds/symlink/pth08080w.pdf (http://www.ti.com/lit/ds/symlink/pth08080w.pdf)
[7] Xilinx, 2016, 7 Series FPGAs and Zynq-7000 All Programmable SoC, XADC Dual 12-Bit 1 MSPS Analog-to-Digital Converter https://www.xilinx.com/support/documentation/user_guides/ug480_7Series_XADC.pdf (https://www.xilinx.com/support/documentation/user_guides/ug480_7Series_XADC.pdf)
[8] ITEAD Intelligent System Co. Ltd., https://www.itead.cc/
[9] Ansmann, 2013, Li-Ion Rechargeable 18650 2S1P, http://www.farnell.com/datasheets/2140411.pdf
[10] RS-Online, 2017, RS Pro Summer 85dB, http://dk.rs-online.com/web/p/magnetisk-brummer-komponenter/5117664/ (http://dk.rs-online.com/web/p/magnetisk-brummer-komponenter/5117664/)
[11] RS-Online, | 2017, | Sonitron | Piezo-hjttalere | 92dB, | http://dk.
rs-online.com/web/p/piezoelektriske-miniaturehojttalere/ 2945630/ (http://dk.rs-online.com/web/p/piezoelektriske-miniaturehojttalere/2945630/)

27

[12] RS-Online, 2017, RS Pro Miniaturehjttaler, http://dk.rs-online.com/web/p/miniature-hojttalere/7564595/ (http://dk.rs-online.com/web/p/miniature-hojttalere/7564595/)
[13] Jaedicke, Mikkel S., Christensen, Thomas S., SDU-Embedded, June 2017, Schematic and Layout for the Swarmbot Carrier Card, https://github.com/SDU-Embedded/swarmbot_carrier/blob/master/documentation/swarmbot_rev5.pdf (https://github.com/SDU-Embedded/swarmbot_carrier/blob/master/documentation/swarmbot_rev5.pdf)
[14] Jaedicke, Mikkel S., Christensen, Thomas S., SDU-Embedded, June 2017, Swarmbot Carrier Card Github, https://github.com/SDU-Embedded/swarmbot_carrier (https://github.com/SDU-Embedded/swarmbot_carrier)
[15] Jaedicke, Mikkel S., Christensen, Thomas S., SDU-Embedded,
June 2017, | Pinout of the Swarmbot Carrier Card, | https:
//github.com/SDU-Embedded/swarmbot_carrier/tree/master/ documentation/pinout (https://github.com/SDU-Embedded/swarmbot_carrier/tree/master/documentation/pinout)

28

## A Components

29

Table A.1: Components on the MicroZed carrier card and on the SwarmBot carrier card.

# Comment Qty MicroZed Carrier Card SwarmBot Carrier Card Comment

1 Capacitor

7 0805ZD226MAT2A GRM21BR60J226ME39L Found equivalent capacitor as

the original comes in packages

of 3000.

2 DNP

3 Capacitor

8 06035C104KAT2A GCM21BR71H104KA02L Found equivalent capacitor

with 0805 footprint

4 Capacitor

4 04023C104KAT2A C0805C103K5RACTU Original was out of stock.
Found equivalent capacitor

with 0805 footprint

5 Connector Equivalent ones will be found

at the component storage at

SDU

6 MicroUSB 1 1981584-1 47589-0001 Original needs to be bought in

packs of 10. Found a cheaper
equivalent one that can be

bought in packs of 5.

7 DNP

8 Schottky
Diode

1 MBR230LSFT1G SBR2A40P1-7 Original only ships in packs of
50. Found a a similiar diode

with. Has a a higher forward
voltage drop, but rough calculations estimate that it will

only decrease the efficiency
with one percentage point.

9 Schottky
Diode

2 BAT54LT1G SBR2A40P1-7 The SBR2A40P1-7 diode is

better in all aspects and 25 of
them are already bought for

#8

30

Table A.2: Components on the MicroZed carrier card and on the SwarmBot carrier card.

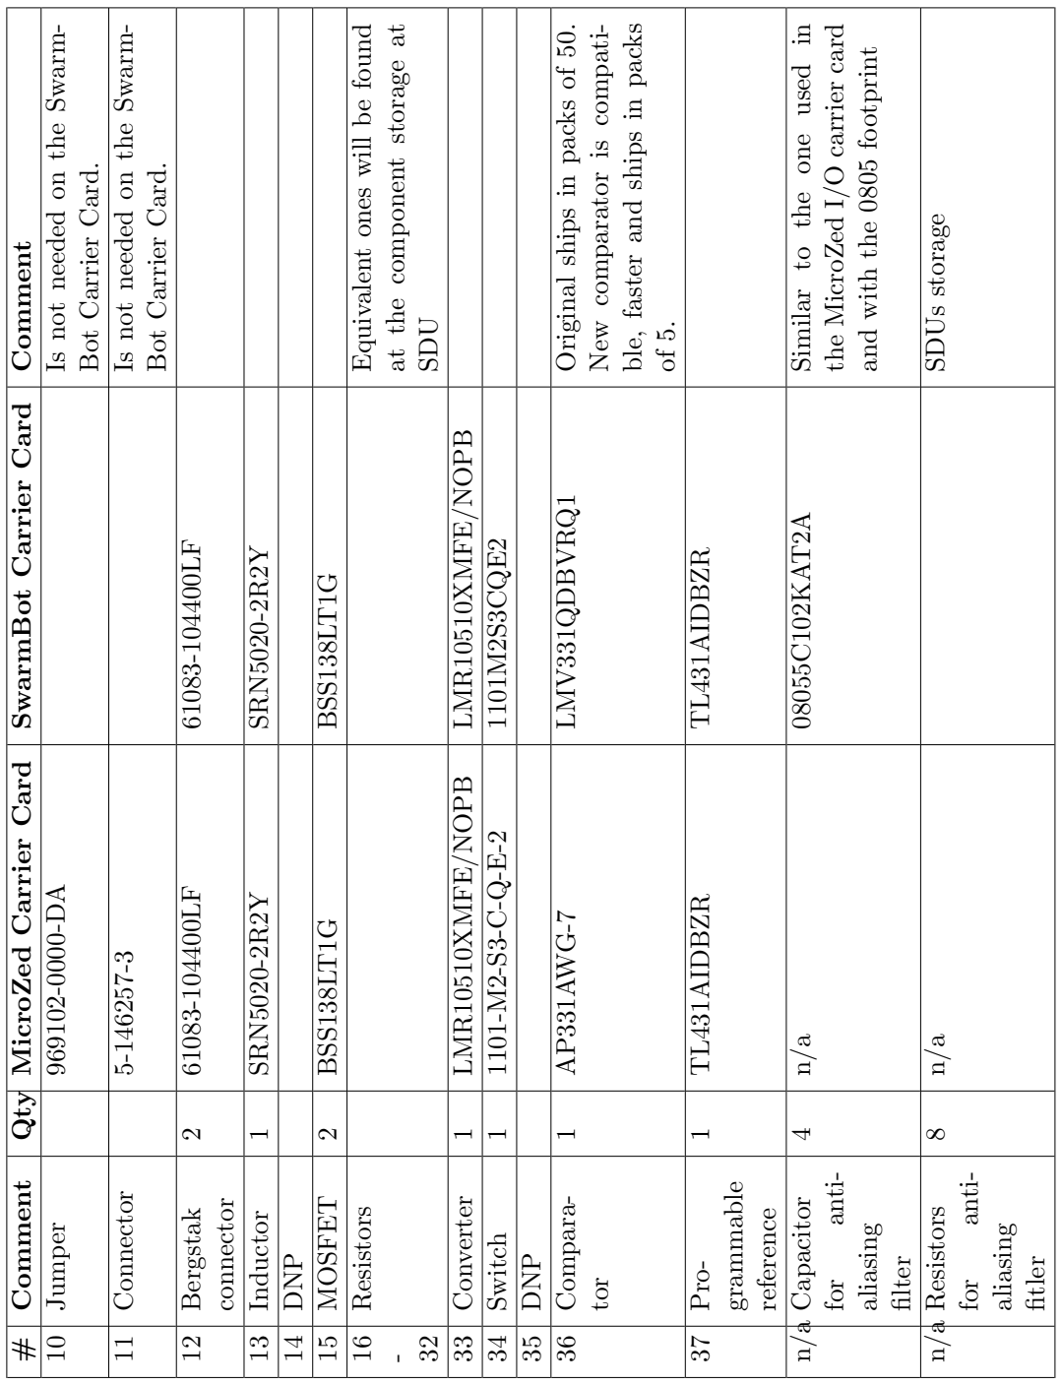
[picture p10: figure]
Bot Carrier Card.; 12 Bergstak; connector; 13 Inductor 1 SRN5020-2R2Y SRN5020-2R2Y; 14 DNP; 15 MOSFET 2 BSS138LT1G BSS138LT1G; Resistors Equivalent ones will be found; at the component storage at; SDU; 35 DNP; 36 Compara-; tor; New comparator is compati-; ble, faster and ships in packs; 37 Pro-; grammable; reference; 1 TL431AIDBZR TL431AIDBZR; n/a Capacitor; for anti-; aliasing; filter; the MicroZed I/O carrier card; and with the 0805 footprint; n/a Resistors; fitler; 8 n/a SDUs storage

# Comment Qty MicroZed Carrier Card SwarmBot Carrier Card Comment

10 Jumper 969102-0000-DA Is not needed on the Swarm-

11 Connector 5-146257-3 Is not needed on the Swarm-

33 Converter 1 LMR10510XMFE/NOPB LMR10510XMFE/NOPB

34 Switch 1 1101-M2-S3-C-Q-E-2 1101M2S3CQE2

1 AP331AWG-7 LMV331QDBVRQ1 Original ships in packs of 50.

4 n/a 08055C102KAT2A Similar to the one used in

31

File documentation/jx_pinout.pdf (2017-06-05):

JX1 Pin | MicroZed Net Name | Zynq Pin | Zynq Name | Swarmbot Net
1 | JTAG_TCK | F9 | TCK_0 | -
2 | JTAG_TMS | J6 | TMS_0 | -
3 | JTAG_TDO | F6 | TDO_0 | -
4 | JTAG_TDI | G6 | TDI_0 | -
5 | NetJX1_5 | - | - | PWR_EN
6 | NetJX1_6 | - | - | -
7 | FPGA_VBATT | F11 | VCCBATT_0 | -
8 | FPGA_DONE | R11 | DONE_0 | FPGA_DONE
9 | JX1_SE_0 | R19 | IO_0_34 | JX1_IO00
10 | JX1_SE_1 | T19 | IO_25_34 | JX1_IO01
11 | JX1_LVDS_0_P | T11 | IO_L1P_T0_34 | JX1_IO02
12 | JX1_LVDS_1_P | T12 | IO_L2P_T0_34 | JX1_IO03
13 | JX1_LVDS_0_N | T10 | IO_L1N_T0_34 | JX1_IO04
14 | JX1_LVDS_1_N | U12 | IO_L2N_T0_34 | JX1_IO05
15 | GND | A8 | GND | GND
16 | GND | A8 | GND | GND
17 | JX1_LVDS_2_P | U13 | IO_L3P_T0_DQS_PUDC_B_34 | JX1_IO06
18 | JX1_LVDS_3_P | V12 | IO_L4P_T0_34 | JX1_IO07
19 | JX1_LVDS_2_N | V13 | IO_L3N_T0_DQS_34 | JX1_IO08
20 | JX1_LVDS_3_N | W13 | IO_L4N_T0_34 | JX1_IO09
21 | GND | A8 | GND | GND
22 | GND | A8 | GND | GND
23 | JX1_LVDS_4_P | T14 | IO_L5P_T0_34 | JX1_IO10
24 | JX1_LVDS_5_P | P14 | IO_L6P_T0_34 | JX1_IO11
25 | JX1_LVDS_4_N | T15 | IO_L5N_T0_34 | JX1_IO12
26 | JX1_LVDS_5_N | R14 | IO_L6N_T0_VREF_34 | JX1_IO13
27 | GND | A8 | GND | GND
28 | GND | A8 | GND | GND
29 | JX1_LVDS_6_P | Y16 | IO_L7P_T1_34 | JX1_IO14
30 | JX1_LVDS_7_P | W14 | IO_L8P_T1_34 | JX1_IO15
31 | JX1_LVDS_6_N | Y17 | IO_L7N_T1_34 | JX1_IO16
32 | JX1_LVDS_7_N | Y14 | IO_L8N_T1_34 | JX1_IO17
33 | GND | A8 | GND | GND
34 | GND | A8 | GND | GND
35 | JX1_LVDS_8_P | T16 | IO_L9P_T1_DQS_34 | JX1_IO18
36 | JX1_LVDS_9_P | V15 | IO_L10P_T1_34 | JX1_IO19
37 | JX1_LVDS_8_N | U17 | IO_L9N_T1_DQS_34 | JX1_IO20
38 | JX1_LVDS_9_N | W15 | IO_L10N_T1_34 | JX1_IO21
39 | GND | A8 | GND | GND
40 | GND | A8 | GND | GND
41 | JX1_LVDS_10_P | U14 | IO_L11P_T1_SRCC_34 | JX1_IO22
42 | JX1_LVDS_11_P | U18 | IO_L12P_T1_MRCC_34 | JX1_IO23
43 | JX1_LVDS_10_N | U15 | IO_L11N_T1_SRCC_34 | JX1_IO24
44 | JX1_LVDS_11_N | U19 | IO_L12N_T1_MRCC_34 | JX1_IO25
45 | GND | A8 | GND | GND
46 | GND | A8 | GND | GND
47 | JX1_LVDS_12_P | N18 | IO_L13P_T2_MRCC_34 | JX1_IO26

48 | JX1_LVDS_13_P | N20 | IO_L14P_T2_SRCC_34 | JX1_IO27
49 | JX1_LVDS_12_N | P19 | IO_L13N_T2_MRCC_34 | JX1_IO28
50 | JX1_LVDS_13_N | P20 | IO_L14N_T2_SRCC_34 | JX1_IO29
51 | GND | A8 | GND | GND
52 | GND | A8 | GND | GND
53 | JX1_LVDS_14_P | T20 | IO_L15P_T2_DQS_34 | JX1_IO30
54 | JX1_LVDS_15_P | V20 | IO_L16P_T2_34 | JX1_IO31
55 | JX1_LVDS_14_N | U20 | IO_L15N_T2_DQS_34 | JX1_IO32
56 | JX1_LVDS_15_N | W20 | IO_L16N_T2_34 | JX1_IO33
57 | VIN_HDR | #N/A | #N/A | VCC
58 | VIN_HDR | #N/A | #N/A | VCC
59 | VIN_HDR | #N/A | #N/A | VCC
60 | VIN_HDR | #N/A | #N/A | VCC
61 | JX1_LVDS_16_P | Y18 | IO_L17P_T2_34 | JX1_IO34
62 | JX1_LVDS_17_P | V16 | IO_L18P_T2_34 | JX1_IO35
63 | JX1_LVDS_16_N | Y19 | IO_L17N_T2_34 | JX1_IO36
64 | JX1_LVDS_17_N | W16 | IO_L18N_T2_34 | JX1_IO37
65 | GND | A8 | GND | GND
66 | GND | A8 | GND | GND
67 | JX1_LVDS_18_P | R16 | IO_L19P_T3_34 | JX1_IO38
68 | JX1_LVDS_19_P | T17 | IO_L20P_T3_34 | JX1_IO39
69 | JX1_LVDS_18_N | R17 | IO_L19N_T3_VREF_34 | JX1_IO40
70 | JX1_LVDS_19_N | R18 | IO_L20N_T3_34 | JX1_IO41
71 | GND | A8 | GND | GND
72 | GND | A8 | GND | GND
73 | JX1_LVDS_20_P | V17 | IO_L21P_T3_DQS_34 | JX1_IO42
74 | JX1_LVDS_21_P | W18 | IO_L22P_T3_34 | MIC_CM_CLK
75 | JX1_LVDS_20_N | V18 | IO_L21N_T3_DQS_34 | MIC_SCL
76 | JX1_LVDS_21_N | W19 | IO_L22N_T3_34 | MIC_SDA
77 | GND | A8 | GND | GND
78 | VCCO_34 | N19 | VCCO_34 | VCCIO
79 | VCCO_34 | N19 | VCCO_34 | VCCIO
80 | VCCO_34 | N19 | VCCO_34 | VCCIO
81 | JX1_LVDS_22_P | N17 | IO_L23P_T3_34 | MIC_DATA0
82 | JX1_LVDS_23_P | P15 | IO_L24P_T3_34 | MIC_DATA1
83 | JX1_LVDS_22_N | P18 | IO_L23N_T3_34 | MIC_DATA2
84 | JX1_LVDS_23_N | P16 | IO_L24N_T3_34 | MIC_DATA3
85 | GND | A8 | GND | GND
86 | GND | A8 | GND | GND
87 | BANK13_LVDS_0_P | U7 | IO_L11P_T1_SRCC_13 | RGB00
88 | BANK13_LVDS_1_P | T9 | IO_L12P_T1_MRCC_13 | RGB01
89 | BANK13_LVDS_0_N | V7 | IO_L11N_T1_SRCC_13 | RGB02
90 | BANK13_LVDS_1_N | U10 | IO_L12N_T1_MRCC_13 | RGB03
91 | BANK13_LVDS_2_P | V8 | IO_L15P_T2_DQS_13 | RGB04
92 | BANK13_LVDS_3_P | T5 | IO_L19P_T3_13 | RGB05
93 | BANK13_LVDS_2_N | W8 | IO_L15N_T2_DQS_13 | JX1_TP00
94 | BANK13_LVDS_3_N | U5 | IO_L19N_T3_VREF_13 | JX1_TP01
95 | GND | A8 | GND | GND
96 | GND | A8 | GND | GND
97 | NetJX1_97 | K9 | VP_0 | JX1_ADC_P0

98 | NetJX1_98 | M9 | DXP_0 | GND
99 | NetJX1_99 | L10 | VN_0 | JX1_ADC_N0
100 | NetJX1_100 | M10 | DXN_0 | GND

JX2 Pin | MicroZed Net Name | Zynq Pin | Zynq Name | Swarmbot Net
1 | PMOD_D0 | E8 | PS_MIO13_500 | -
2 | PMOD_D1 | E9 | PS_MIO10_500 | -
3 | PMOD_D2 | C6 | PS_MIO11_500 | -
4 | PMOD_D3 | D9 | PS_MIO12_500 | -
5 | #VALUE! | #VALUE! | #VALUE! | -
6 | PMOD_D5 | B5 | PS_MIO9_500 | -
7 | PMOD_D6 | C5 | PS_MIO14_500 | -
8 | PMOD_D7 | C8 | PS_MIO15_500 | -
9 | NetJX2_9 | R10 | INIT_B_0 | -
10 | NetJX2_10 | L6 | PROGRAM_B_0 | VCCIO_EN
11 | PG_MODULE | C7 | PS_POR_B_500 | PG_MODULE
12 | VIN_HDR | #N/A | #N/A | VCC
13 | JX2_SE_0 | G14 | IO_0_35 | JX2_IO00
14 | JX2_SE_1 | J15 | IO_25_35 | BUZ_PWM0
15 | GND | A8 | GND | GND
16 | GND | A8 | GND | GND
17 | JX2_LVDS_0_P | C20 | IO_L1P_T0_AD0P_35 | JX2_IO01
18 | JX2_LVDS_1_P | B19 | IO_L2P_T0_AD8P_35 | BUZ_PWM1
19 | JX2_LVDS_0_N | B20 | IO_L1N_T0_AD0N_35 | JX2_IO02
20 | JX2_LVDS_1_N | A20 | IO_L2N_T0_AD8N_35 | JX2_IO03
21 | GND | A8 | GND | GND
22 | GND | A8 | GND | GND
23 | JX2_LVDS_2_P | E17 | IO_L3P_T0_DQS_AD1P_35 | JX2_IO04
24 | JX2_LVDS_3_P | D19 | IO_L4P_T0_35 | JX2_IO05
25 | JX2_LVDS_2_N | D18 | IO_L3N_T0_DQS_AD1N_35 | JX2_IO06
26 | JX2_LVDS_3_N | D20 | IO_L4N_T0_35 | JX2_IO07
27 | GND | A8 | GND | GND
28 | GND | A8 | GND | GND
29 | JX2_LVDS_4_P | E18 | IO_L5P_T0_AD9P_35 | JX2_IO8
30 | JX2_LVDS_5_P | F16 | IO_L6P_T0_35 | JX2_IO9
31 | JX2_LVDS_4_N | E19 | IO_L5N_T0_AD9N_35 | JX2_IO10
32 | JX2_LVDS_5_N | F17 | IO_L6N_T0_VREF_35 | JX2_IO11
33 | GND | A8 | GND | GND
34 | GND | A8 | GND | GND
35 | JX2_LVDS_6_P | L19 | IO_L9P_T1_DQS_AD3P_35 | JX2_IO12
36 | JX2_LVDS_7_P | M19 | IO_L7P_T1_AD2P_35 | JX2_IO13
37 | JX2_LVDS_6_N | L20 | IO_L9N_T1_DQS_AD3N_35 | JX2_IO14
38 | JX2_LVDS_7_N | M20 | IO_L7N_T1_AD2N_35 | JX2_IO15
39 | GND | A8 | GND | GND
40 | GND | A8 | GND | GND
41 | JX2_LVDS_8_P | M17 | IO_L8P_T1_AD10P_35 | JX2_IO16
42 | JX2_LVDS_9_P | K19 | IO_L10P_T1_AD11P_35 | JX2_IO17
43 | JX2_LVDS_8_N | M18 | IO_L8N_T1_AD10N_35 | JX2_IO18
44 | JX2_LVDS_9_N | J19 | IO_L10N_T1_AD11N_35 | JX2_IO19

45 | GND | A8 | GND | GND
46 | GND | A8 | GND | GND
47 | JX2_LVDS_10_P | L16 | IO_L11P_T1_SRCC_35 | JX2_IO20
48 | JX2_LVDS_11_P | K17 | IO_L12P_T1_MRCC_35 | JX2_IO21
49 | JX2_LVDS_10_N | L17 | IO_L11N_T1_SRCC_35 | JX2_IO22
50 | JX2_LVDS_11_N | K18 | IO_L12N_T1_MRCC_35 | JX2_IO23
51 | GND | A8 | GND | GND
52 | GND | A8 | GND | GND
53 | JX2_LVDS_12_P | H16 | IO_L13P_T2_MRCC_35 | JX2_IO24
54 | JX2_LVDS_13_P | J18 | IO_L14P_T2_AD4P_SRCC_35 | JX2_IO25
55 | JX2_LVDS_12_N | H17 | IO_L13N_T2_MRCC_35 | JX2_IO26
56 | JX2_LVDS_13_N | H18 | IO_L14N_T2_AD4N_SRCC_35 | JX2_IO27
57 | VIN_HDR | #N/A | #N/A | VIN
58 | VIN_HDR | #N/A | #N/A | VIN
59 | VIN_HDR | #N/A | #N/A | VIN
60 | VIN_HDR | #N/A | #N/A | VIN
61 | JX2_LVDS_14_P | G17 | IO_L16P_T2_35 | JX2_IO28
62 | JX2_LVDS_15_P | F19 | IO_L15P_T2_DQS_AD12P_35 | JX2_IO29
63 | JX2_LVDS_14_N | G18 | IO_L16N_T2_35 | JX2_IO30
64 | JX2_LVDS_15_N | F20 | IO_L15N_T2_DQS_AD12N_35 | JX2_IO31
65 | GND | A8 | GND | GND
66 | GND | A8 | GND | GND
67 | JX2_LVDS_16_P | G19 | IO_L18P_T2_AD13P_35 | JX2_IO32
68 | JX2_LVDS_17_P | J20 | IO_L17P_T2_AD5P_35 | JX2_IO33
69 | JX2_LVDS_16_N | G20 | IO_L18N_T2_AD13N_35 | JX2_IO34
70 | JX2_LVDS_17_N | H20 | IO_L17N_T2_AD5N_35 | JX2_IO35
71 | GND | A8 | GND | GND
72 | GND | A8 | GND | GND
73 | JX2_LVDS_18_P | K14 | IO_L20P_T3_AD6P_35 | JX2_IO36
74 | JX2_LVDS_19_P | H15 | IO_L19P_T3_35 | JX2_ADC_P1
75 | JX2_LVDS_18_N | J14 | IO_L20N_T3_AD6N_35 | JX2_IO37
76 | JX2_LVDS_19_N | G15 | IO_L19N_T3_VREF_35 | JX2_ADC_N1
77 | GND | A8 | GND | GND
78 | VCCO_35 | C19 | VCCO_35 | VCCIO
79 | VCCO_35 | C19 | VCCO_35 | VCCIO
80 | VCCO_35 | C19 | VCCO_35 | VCCIO
81 | JX2_LVDS_20_P | N15 | IO_L21P_T3_DQS_AD14P_35 | ENC0A
82 | JX2_LVDS_21_P | L14 | IO_L22P_T3_AD7P_35 | JX2_ADC_P2
83 | JX2_LVDS_20_N | N16 | IO_L21N_T3_DQS_AD14N_35 | ENC0B
84 | JX2_LVDS_21_N | L15 | IO_L22N_T3_AD7N_35 | JX2_ADC_N2
85 | GND | A8 | GND | GND
86 | GND | A8 | GND | GND
87 | JX2_LVDS_22_P | M14 | IO_L23P_T3_35 | ENC1A
88 | JX2_LVDS_23_P | K16 | IO_L24P_T3_AD15P_35 | JX2_ADC_P3
89 | JX2_LVDS_22_N | M15 | IO_L23N_T3_35 | ENC1B
90 | JX2_LVDS_23_N | J16 | IO_L24N_T3_AD15N_35 | JX2_ADC_N3
91 | GND | A8 | GND | GND

92 | GND | A8 | GND | GND
93 | BANK13_LVDS_4_P | Y12 | IO_L20P_T3_13 | JX2_IO38
94 | BANK13_LVDS_5_P | V11 | IO_L21P_T3_DQS_13 | JX2_TP00
95 | BANK13_LVDS_4_N | Y13 | IO_L20N_T3_13 | JX2_TP01
96 | BANK13_LVDS_5_N | V10 | IO_L21N_T3_DQS_13 | M0_PWM0
97 | BANK13_LVDS_6_P | V6 | IO_L22P_T3_13 | M1_PWM1
98 | VCCO_13 | T8 | VCCO_13 | VCCIO
99 | BANK13_LVDS_6_N | W6 | IO_L22N_T3_13 | M1_PWM0
100 | BANK13_SE_0 | V5 | IO_L6N_T0_VREF_13 | M0_PWM1

Header Pin | Zynq Pin | Swarmbot Net | Remark
1 | - | GND
2 | - | ENC0A
3 | - | ENC0B
4 | - | VCCIO | 3.3V
5 | - | M0_OUT1
6 | - | M0_OUT2
Header Pin | Zynq Pin | Swarmbot Net | Remark
1 | - | GND
2 | - | ENC1A
3 | - | ENC1B
4 | - | VCCIO | 3.3V
5 | - | M1_OUT1
6 | - | M1_OUT2
Header Pin | Zynq Pin | Swarmbot Net | Remark
1 | - | MIC_DATA3
2 | - | MIC_DATA2
3 | - | MIC_DATA1
4 | - | MIC_DATA0
5 | - | GND
6 | - | VCCIO | 3.3V
7 | - | MIC_CM_CLK
8 | - | MIC_SDA
9 | - | MIC_SCL
10 | - | N/C
11 | - | GND
12 | - | VCCIO | 3.3V
Header Pin | Zynq Pin | Swarmbot Net | Remark
1 | K9 | VAUX_P0 | Connected through anti-aliasing filter
2 | L10 | VAUX_N0
3 | K16 | VAUX_P3
4 | J16 | VAUX_N3
5 | L14 | VAUX_P2
6 | L15 | VAUX_N2
7 | H15 | VAUX_P1
8 | G15 | VAUX_N1
Header Pin | Zynq Pin | Swarmbot Net | Remark
1 | - | VBATT | Battery voltage
2 | - | VCC | 5V
3 | - | VCCIO | 3.3V
4 | - | 2V5REF | 2.5V reference
5 | - | GND
Header Pin | Zynq Pin | Swarmbot Net | Remark
1 | V11 | JX1_TP00

P1 - Power Header

P2 - Test Header

CON2 - M1 Driver Header

CON1 - M0 Driver Header

CON3 - Microphone Header

CON4 - ADC Header

2 | Y13 | JX1_TP01
3 | W8 | JX2_TP00
4 | U5 | JX2_TP01
Header Pin | Zynq Pin | Swarmbot Net | Remark
1 | - | VBATT | Battery voltage
2 | B19 | BUZ_PWM1
3 | J15 | BUZ_PWM0
4 | - | GND

P4 - Audio Header

CON5 Pin | Zynq Pin | Swarmbot Net | Remark
1 | - | GND
2 | - | GND
3 | R19 | JX1_IO00
4 | T19 | JX1_IO01
5 | T11 | JX1_IO02
6 | T12 | JX1_IO03
7 | T10 | JX1_IO04
8 | U12 | JX1_IO05
9 | U13 | JX1_IO06
10 | V12 | JX1_IO07
11 | V13 | JX1_IO08
12 | W13 | JX1_IO09
13 | T14 | JX1_IO10
14 | P14 | JX1_IO11
15 | T15 | JX1_IO12
16 | R14 | JX1_IO13
17 | Y16 | JX1_IO14
18 | W14 | JX1_IO15
19 | Y17 | JX1_IO16
20 | Y14 | JX1_IO17
21 | T16 | JX1_IO18
22 | V15 | JX1_IO19
23 | U17 | JX1_IO20
24 | W15 | JX1_IO21
25 | U14 | JX1_IO22
26 | U18 | JX1_IO23
27 | U15 | JX1_IO24
28 | U19 | JX1_IO25
29 | - | VCC | 5V
30 | - | VCC | 5V
31 | - | GND
32 | - | GND
33 | N18 | JX1_IO26
34 | N20 | JX1_IO27
35 | P19 | JX1_IO28
36 | P20 | JX1_IO29
37 | T20 | JX1_IO30
38 | V20 | JX1_IO31
39 | U20 | JX1_IO32
40 | W20 | JX1_IO33
41 | Y18 | JX1_IO34
42 | V16 | JX1_IO35
43 | Y19 | JX1_IO36
44 | W16 | JX1_IO37
45 | R16 | JX1_IO38
46 | T17 | JX1_IO39
47 | R17 | JX1_IO40
48 | R18 | JX1_IO41

GPIO Header 1 - CON5

49 | V17 | JX1_IO42
50 | W18 | MIC_CM_CLK | Also connected to CON3
51 | V18 | MIC_SCL | Also connected to CON3
52 | W19 | MIC_SDA | Also connected to CON3
53 | N17 | MIC_DATA0 | Also connected to CON3
54 | P15 | MIC_DATA1 | Also connected to CON3
55 | P18 | MIC_DATA2 | Also connected to CON3
56 | P16 | MIC_DATA3 | Also connected to CON3
57 | - | VCCIO | 3.3V
58 | - | VCCIO | 3.3V
59 | - | GND
60 | - | GND

CON6 Pin | Zynq Pin | Swarmbot Net | Remark
1 | - | GND
2 | - | GND
3 | C7 | PG_MODULE
4 | J15 | BUZ_PWM0
5 | G14 | JX2_IO00
6 | B19 | BUZ_PWM1
7 | C20 | JX2_IO01
8 | B20 | JX2_IO02
9 | A20 | JX2_IO03
10 | E17 | JX2_IO04
11 | D19 | JX2_IO05
12 | D18 | JX2_IO06
13 | D20 | JX2_IO07
14 | E18 | JX2_IO08
15 | F16 | JX2_IO09
16 | E19 | JX2_IO10
17 | F17 | JX2_IO11
18 | L19 | JX2_IO12
19 | M19 | JX2_IO13
20 | L20 | JX2_IO14
21 | M20 | JX2_IO15
22 | M17 | JX2_IO16
23 | K19 | JX2_IO17
24 | M18 | JX2_IO18
25 | J19 | JX2_IO19
26 | L16 | JX2_IO20
27 | K17 | JX2_IO21
28 | L17 | JX2_IO22
29 | | VCC | 5V
30 | | VCC | 5V
31 | | GND
32 | | GND
33 | K18 | JX2_IO23
34 | H16 | JX2_IO24
35 | J18 | JX2_IO25
36 | H17 | JX2_IO26
37 | H18 | JX2_IO27
38 | G17 | JX2_IO28
39 | F19 | JX2_IO29
40 | G18 | JX2_IO30
41 | F20 | JX2_IO31
42 | G19 | JX2_IO32
43 | J20 | JX2_IO33
44 | G20 | JX2_IO34
45 | H20 | JX2_IO35
46 | K14 | JX2_IO36
47 | J14 | JX2_IO37
48 | Y12 | JX2_IO38

GPIO Header 2 - CON6

49 | N15 | ENC0A | Also connected to CON1
50 | M15 | ENC1B | Also connected to CON2
51 | N16 | ENC0B | Also connected to CON1
52 | M14 | ENC1A | Also connected to CON2
53 | V10 | M0_PWM0 | Also connected to Q4
54 | V5 | M0_PWM1 | Also connected to Q4
55 | W6 | M1_PWM0 | Also connected to Q8
56 | V6 | M1_PWM1 | Also connected to Q8
57 | - | VCCIO | 3.3V
58 | - | VCCIO | 3.3V
59 | - | GND
60 | - | GND

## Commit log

2017-05-22 Added swarmbot carrier card altium project to git repository
    [swarmbot.PrjPcb]
2017-05-22 Fixed some routing
    [carrier_card.PcbDoc]
2017-05-22 Added dimensions to pcb, updated revision numbers on schematics
    [carrier_card.PcbDoc, carrier_card_s3.SchDoc]
2017-06-05 More dimensions on PCB, changed EN to IN on PTH08080 component.
    [carrier_card.PcbDoc, carrier_card_s2.SchDoc, swarmbot.PrjPcb]
2017-06-05 added swarmbot carrier card schematic and layout
